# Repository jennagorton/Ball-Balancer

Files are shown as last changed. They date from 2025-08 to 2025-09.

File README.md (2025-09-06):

<h1 align="center">Ball Balancing Robot</h1>
<p align="center">Jenna Gorton, August 2025</p>

<p align="center">
  workingTest
</p>
<p align="center">Stabilizing at center</p>

-----

About 
= 
I designed and built a 3RRS parallel manipulator to stabilize a ball on a platform. To complete this project, I developed the robot in CAD, derived the inverse kinematic model, and used a PID algorithm to control the robot.

Files
=
- **`Main.ino`** - Runs the code on the arduino
- **`InverseKinematics.cpp`** - Uses the target tilt angles of the platform to calculate the servo angles
- **`ScreenControl.cpp`** - Finds the calibrated position of the ball
- **`ServoControl.cpp`** - Handles smooth movement of the servos
- **`PID.cpp`** - Creates the PID equations based on the target point and the current location of the ball

Design
=
This robot was designed using CAD and then 3D printed with PLA
- This robot has a servo to control each leg of the 3RRS parallel manipulator. The lower limb of the leg has a rotational joint attached to the servo and upper limb, and the upper limb connects to the platform with a spherical joint.
- On the platform, there is a 4-wire resistive touch screen to track the position of the ball

Programming
=
The code was written in C++, then compiled and executed through an Arduino sketch
- The inverse kinematic model was hand-derived, and the equations were implemented in C++. The inputs are the height of the platform and the tilt of the platform in the X and Y directions.
- Two PID controllers are running simultaneously, one handles the tilt in the Y direction and the other handles the tilt in the X direction. Different gain constants were used when the ball was near the target and far away. The gain constants were carefully tuned by hand until the movement was smooth and precise.

Patterns
=
Four different pattern modes continuously move the target balance point around the platform. The modes can be changed by pressing a button, and the screen displays the current mode.

| <div align="center">GIF 1<br>**Ellipse Pattern**</div> | <div align="center">GIF 2<br>**Line Pattern**</div> |
|---|---|
| <div align="center">GIF 3<br>**Figure 8 Pattern**</div> | <div align="center">GIF 4<br>**Triangle Pattern**</div> |

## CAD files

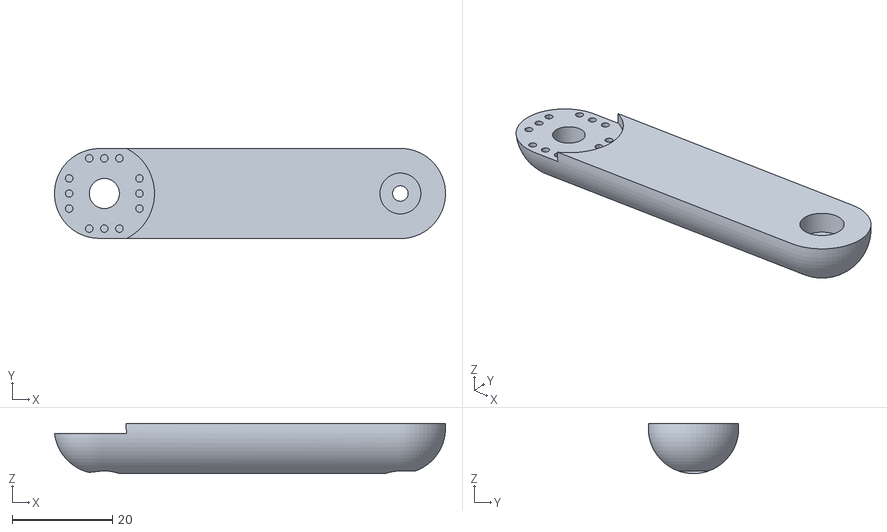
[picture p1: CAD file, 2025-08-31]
STL Files/L1 - Part 1 8.stl
77.9 x 18.0 x 10.0

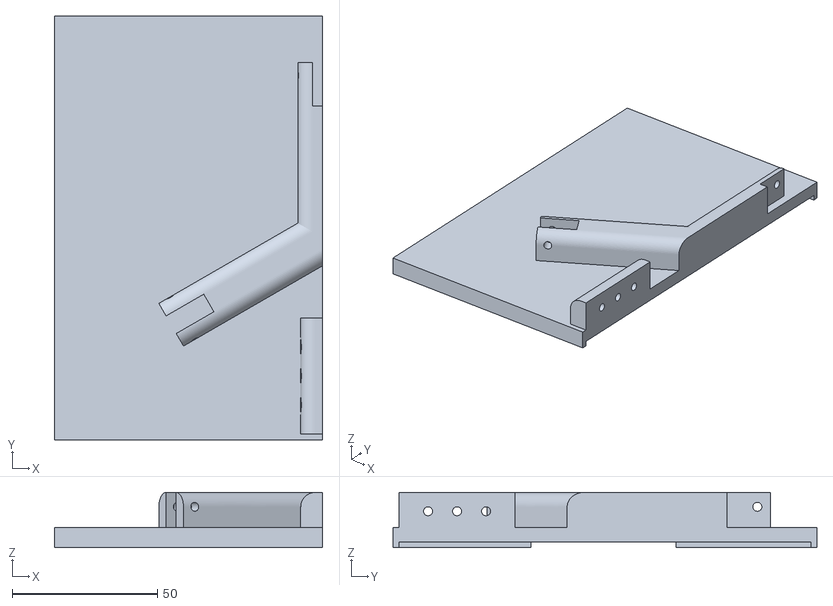
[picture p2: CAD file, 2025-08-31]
STL Files/Platform - Part 2.stl
92.4 x 146.0 x 19.0

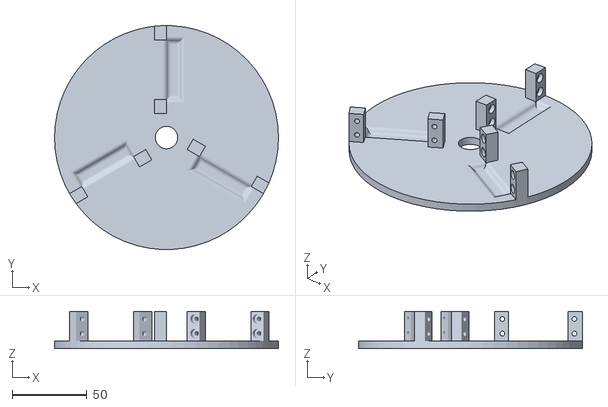
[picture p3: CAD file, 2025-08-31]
STL Files/Base - Part 1 7.stl
150.0 x 149.9 x 25.0

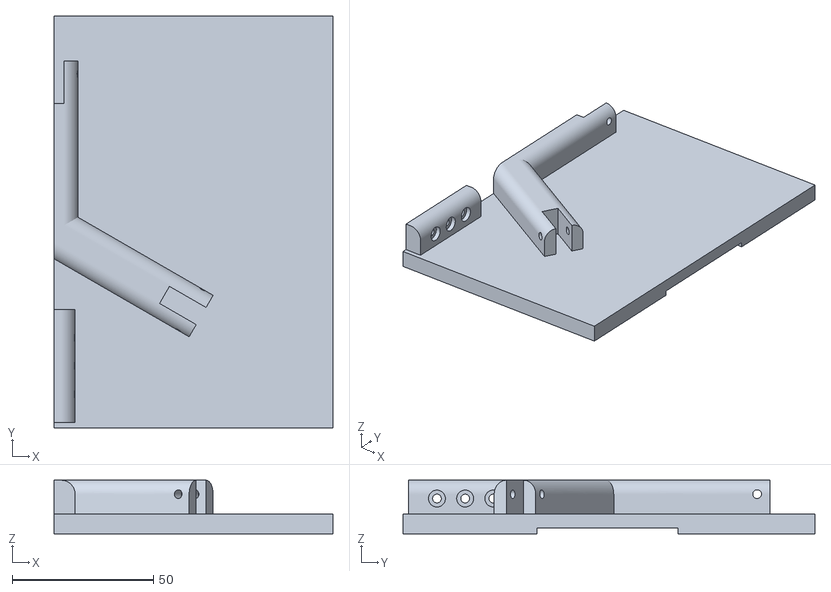
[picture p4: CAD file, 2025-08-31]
STL Files/Platform - Part 1.stl
98.9 x 146.0 x 19.0

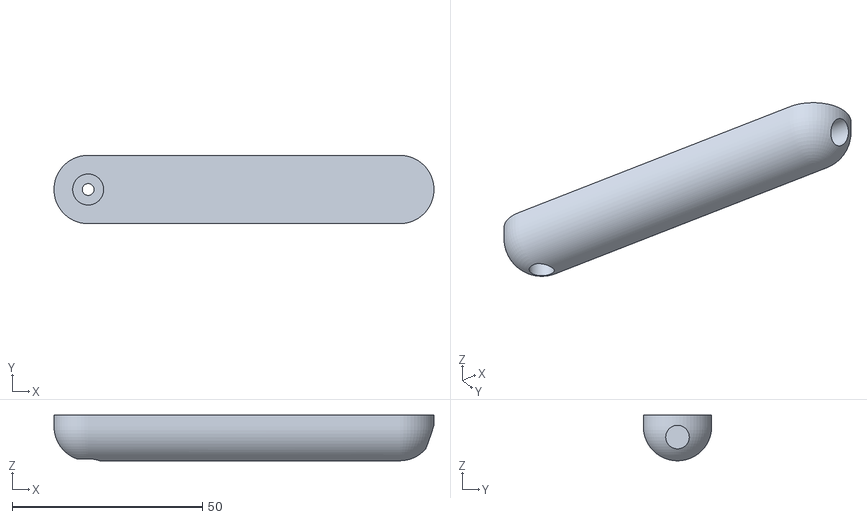
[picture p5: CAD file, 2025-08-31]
STL Files/L2 - Part 1 8.stl
100.0 x 18.0 x 12.0

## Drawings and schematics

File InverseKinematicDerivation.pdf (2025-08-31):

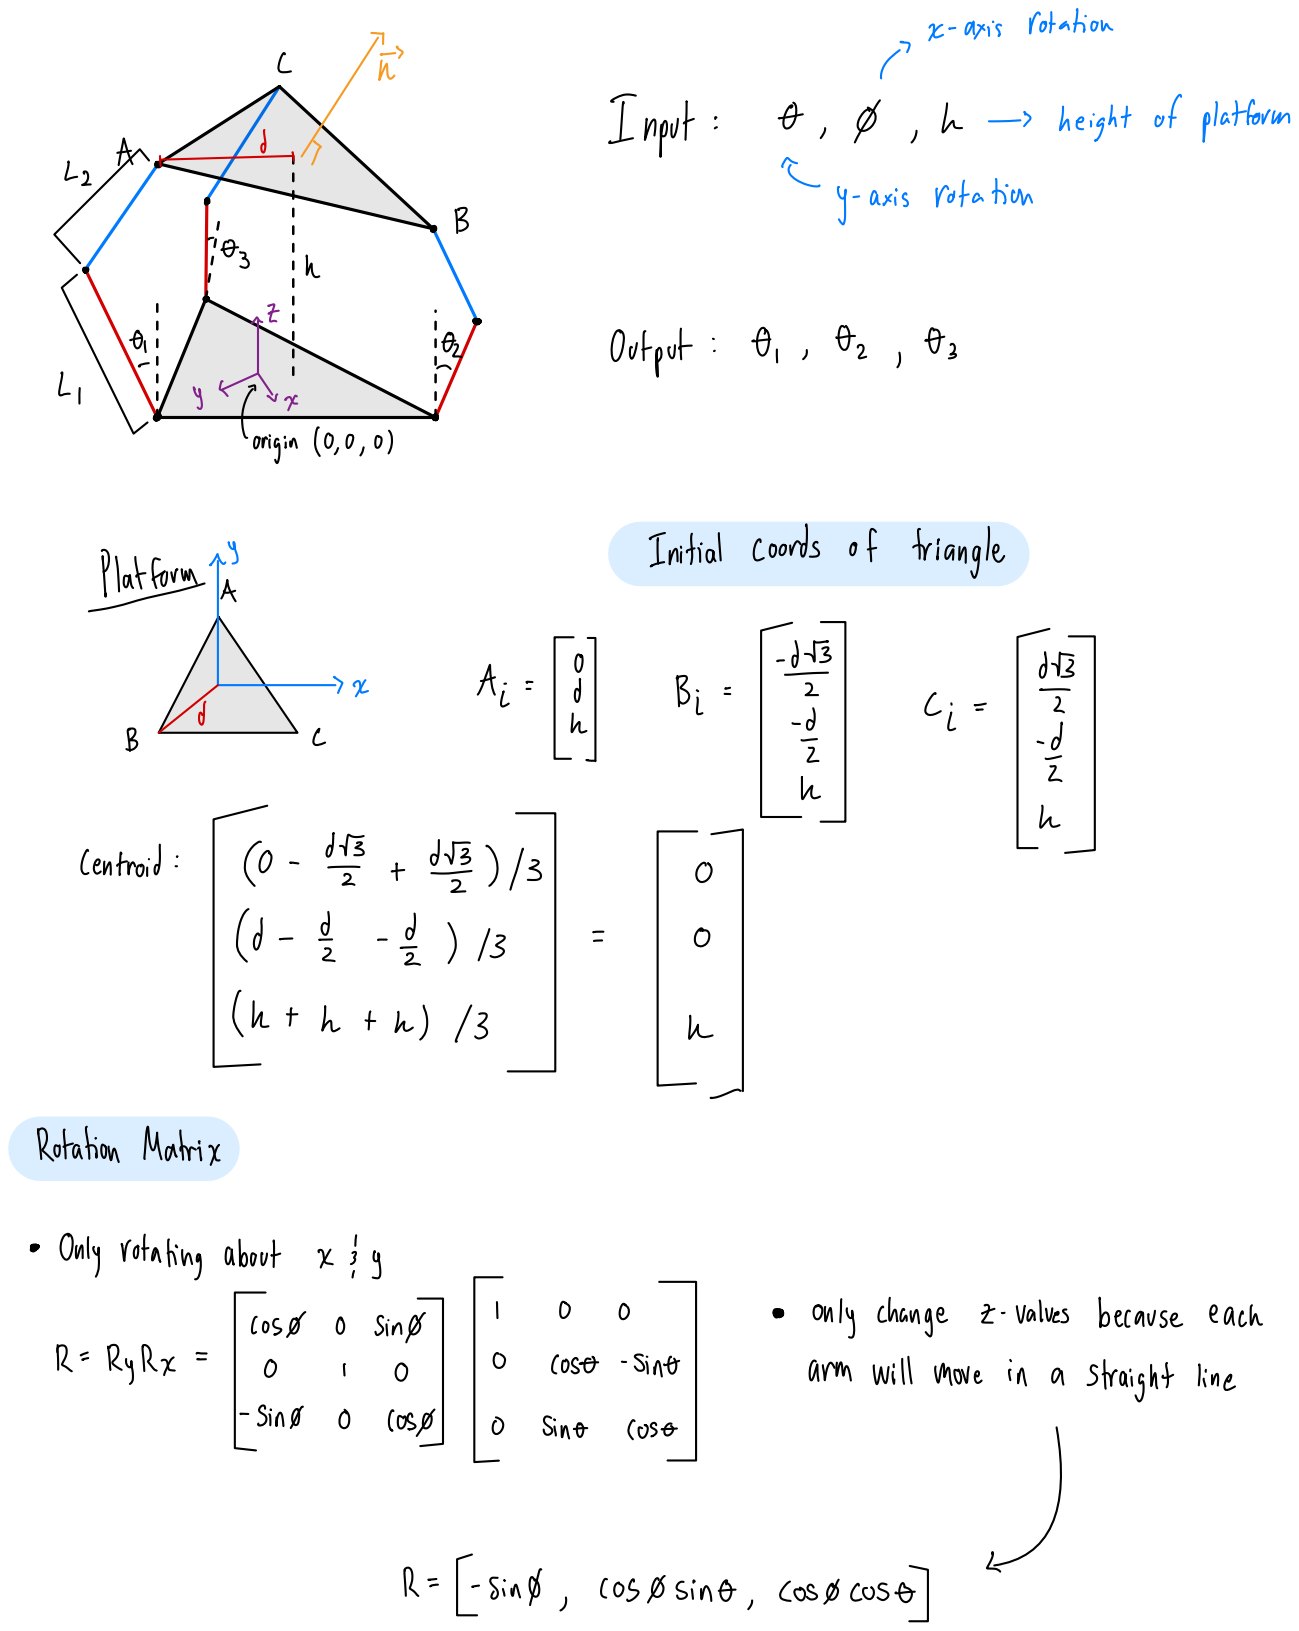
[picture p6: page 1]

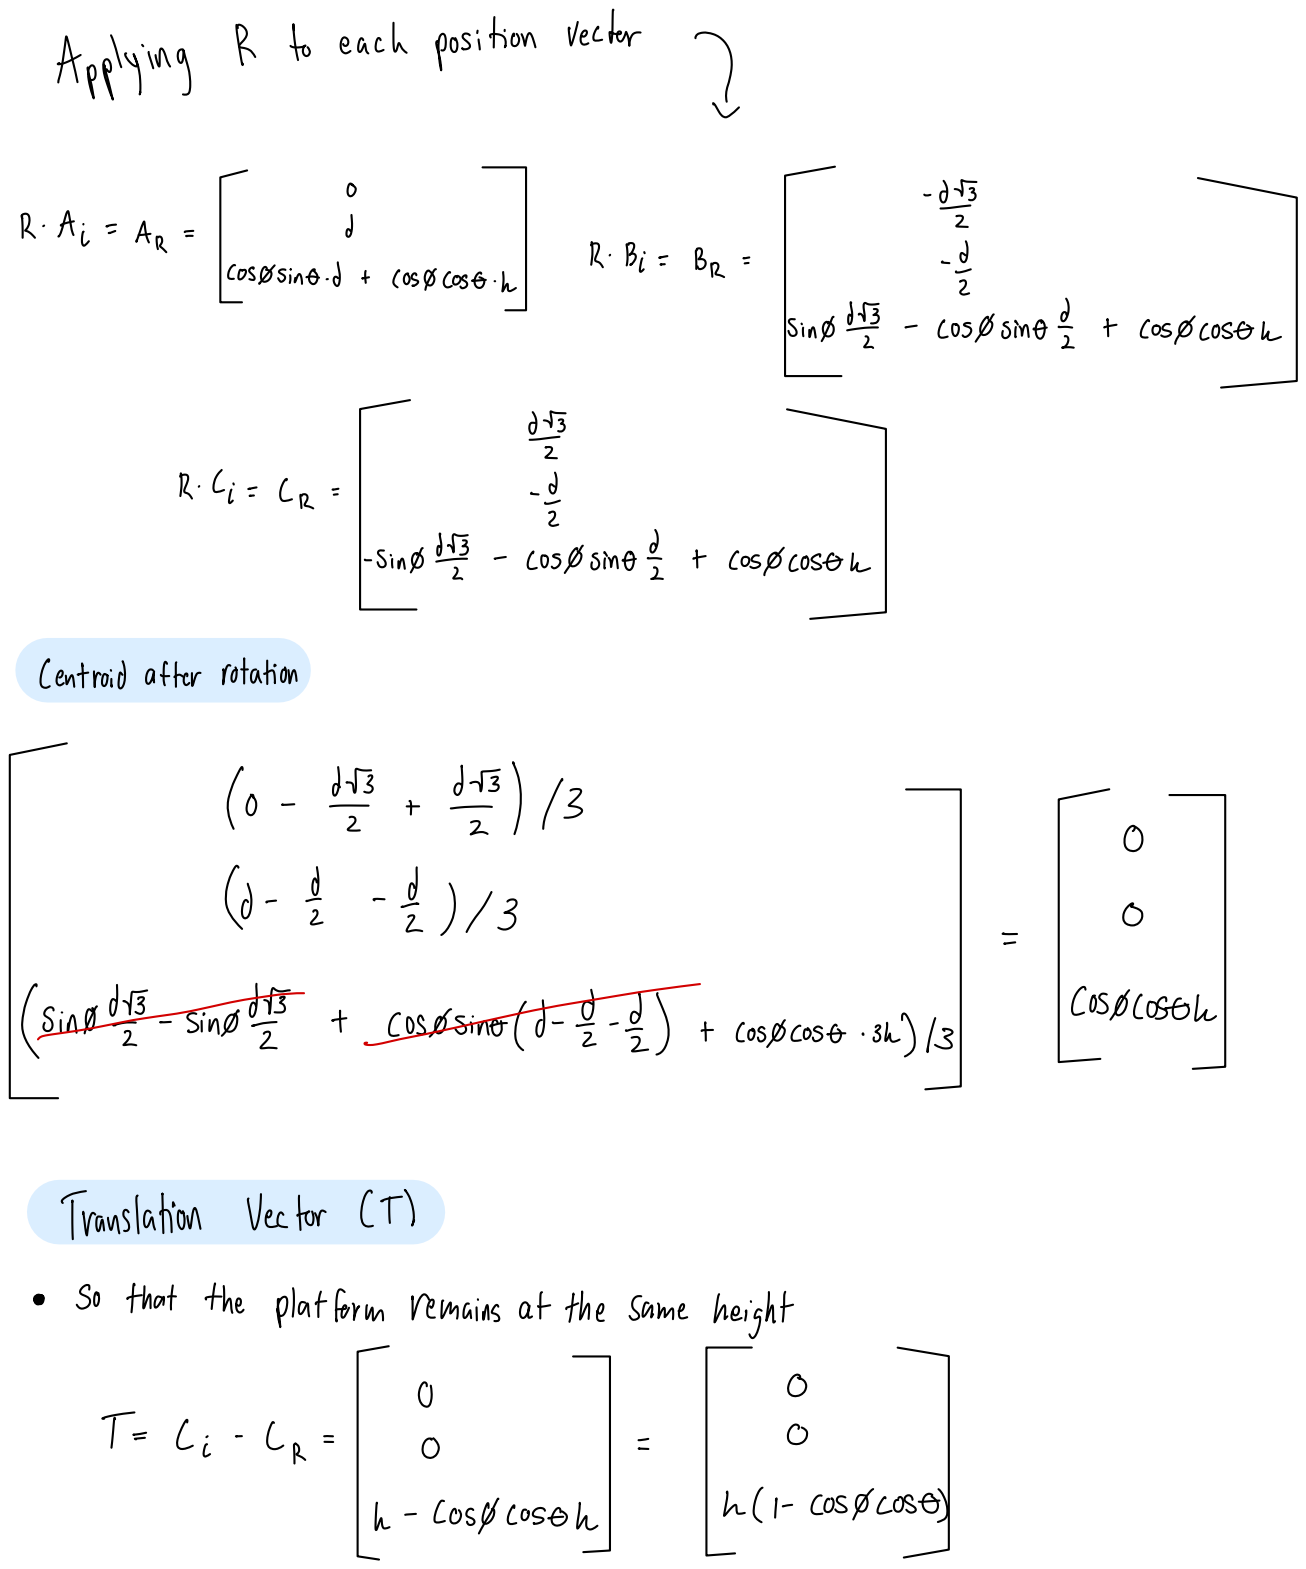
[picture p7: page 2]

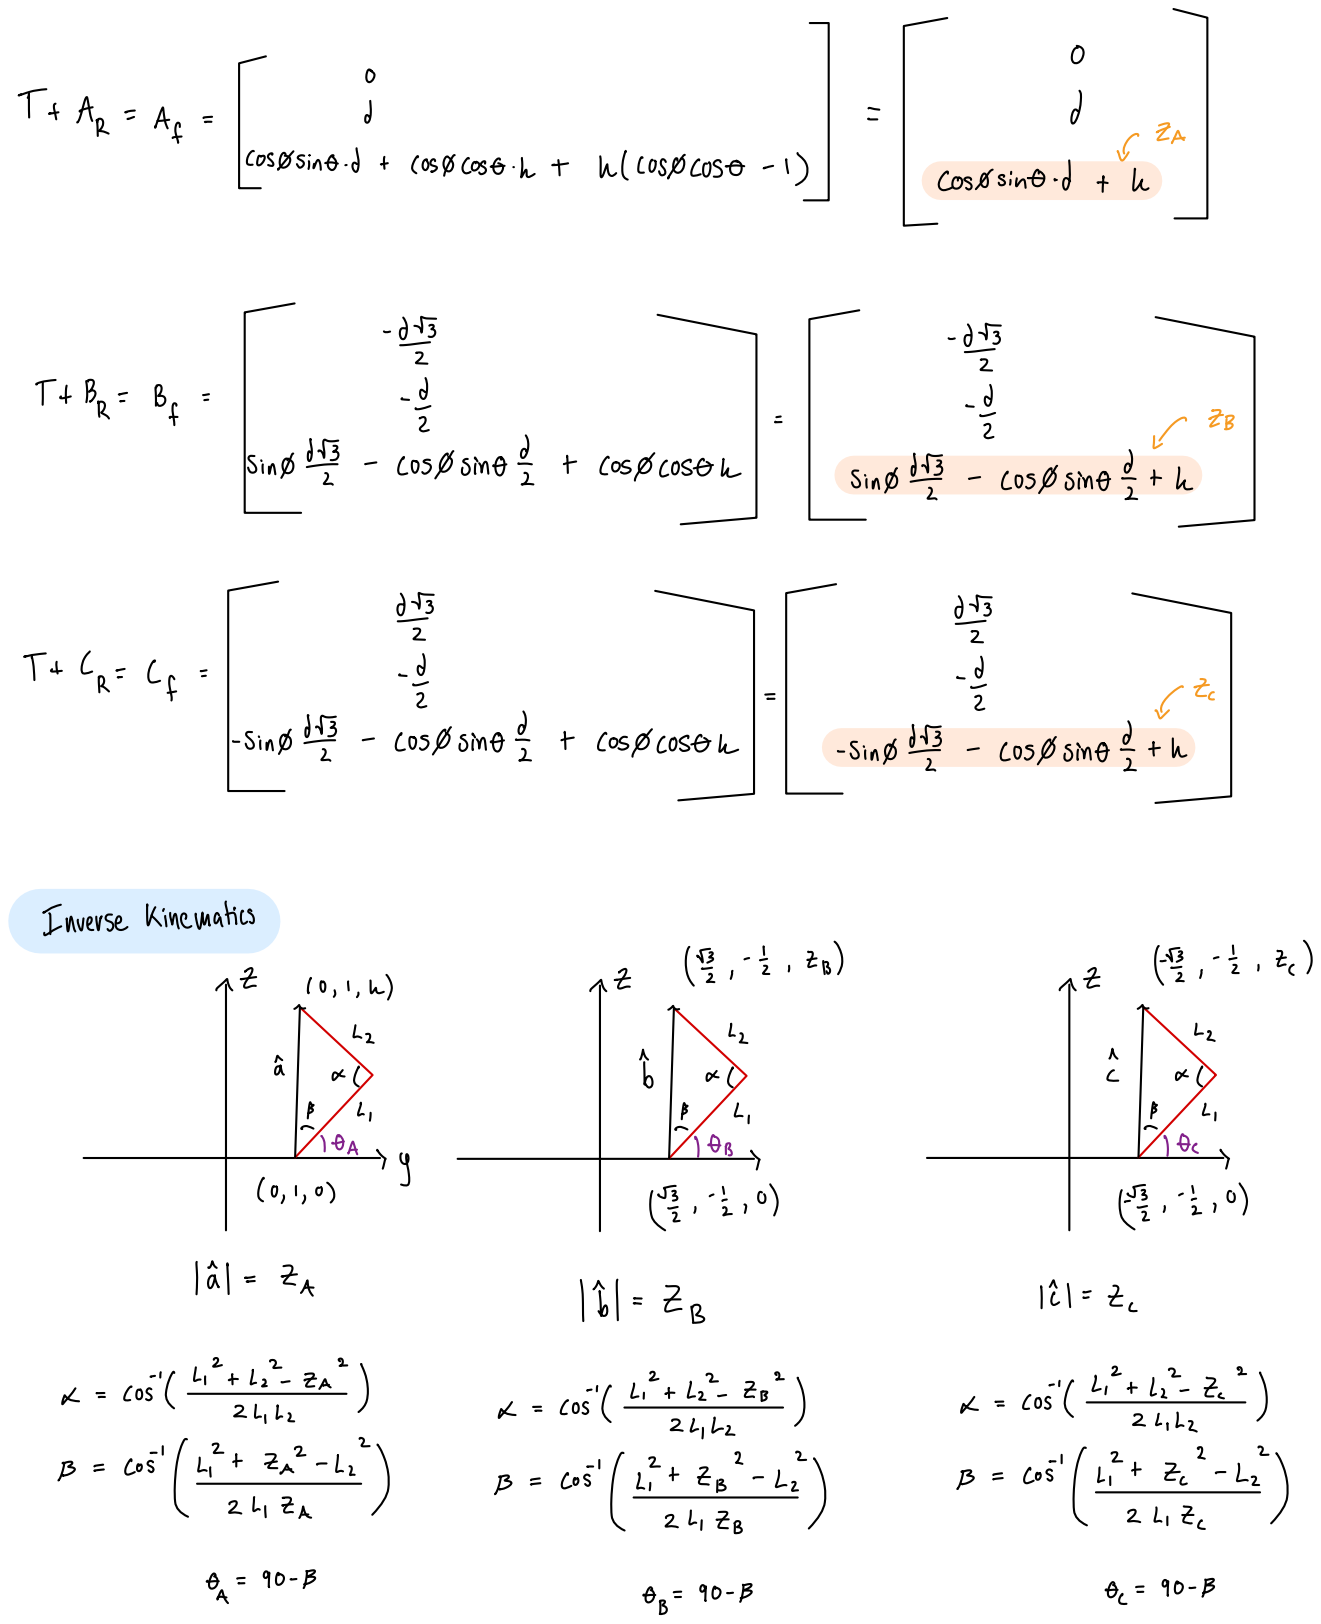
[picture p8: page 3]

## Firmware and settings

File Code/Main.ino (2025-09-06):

#include <Arduino.h>
#include "InverseKinematics.h"
#include "ServoControl.h"
#include "ScreenControl.h"
#include "PID.h"
#include <Wire.h>
#include <Adafruit_GFX.h>
#include <Adafruit_SSD1306.h>

// -------------------- OLED Setup --------------------
#define SCREEN_WIDTH 128
#define SCREEN_HEIGHT 64
Adafruit_SSD1306 display(SCREEN_WIDTH, SCREEN_HEIGHT, &Wire, -1);

const int buttonPin = 2; 
int buttonState = 0;
int lastButtonState = 0;
int mode = 0; // 0=balance, 1=ellipse, 2=line, 3=figure 8, 4=triangle
int lastMode = -1;


void setup() {
  // Initialization functions
  Serial.begin(115200);
  screen_init();
  servo_init();
  pinMode(buttonPin, INPUT_PULLUP);

  if(!display.begin(SSD1306_SWITCHCAPVCC, 0x3C)){
    Serial.println("SSD1306 allocation failed");
    for(;;);
  }
  display.clearDisplay();
}

void loop() {

  buttonState = digitalRead(buttonPin);

  //detects button transition
  if (buttonState == LOW && lastButtonState == HIGH) {
    mode = (mode + 1) % 5;
    Serial.print("Mode changed to: ");
    Serial.println(mode);
    delay(50);              
  }

  if(mode != lastMode){
    updateOLED(mode);
    lastMode = mode;
  }

  //changes pattern based on button press
  switch (mode) {
    case 0:
      balance(0, 0);
      break;
    case 1:
      ellipse(20, 20, 10);
      break;
    case 2:
      line(50, 0, 750);
      break;
    case 3:
      figure8(40, 20, 3);
      break;
    case 4:
      triangle(5); 
      break;
  }

  lastButtonState = buttonState;
}


//function to write to screen
void updateOLED(int mode) {
  display.clearDisplay();
  display.setTextSize(2);
  display.setTextColor(SSD1306_WHITE);

  const char* text;
  switch(mode){
    case 0: text = "Balance"; break;
    case 1: text = "Ellipse"; break;
    case 2: text = "Line"; break;
    case 3: text = "Figure 8"; break;
    case 4: text = "Triangle"; break;
  }

  int16_t x1, y1;
  uint16_t w, h;
  display.getTextBounds(text, 0, 0, &x1, &y1, &w, &h);

  int16_t x = (SCREEN_WIDTH - w) / 2;
  int16_t y = (SCREEN_HEIGHT - h) / 2;

  display.setCursor(x, y);
  display.println(text);
  display.display();
}

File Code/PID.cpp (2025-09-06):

#include <Arduino.h>
#include <math.h>
#include "PID.h"

// PID Constants
#define kp_far_x 0.8
#define ki_far_x 0.15 
#define kd_far_x 0.27

#define kp_far_y 0.6
#define ki_far_y 0.15
#define kd_far_y 0.26

#define kp_close_x .18
#define ki_close_x 0.15
#define kd_close_x 0.23

#define kp_close_y .12
#define ki_close_y 0.15
#define kd_close_y 0.235

#define max_output 83.5  // max X distance away from the center
#define max_angle 12.5   // max tilt angle
const double height = 85; // height of platform

//Array definition
double error[2] = { 0, 0 };
double error_prev[2];
double integral[2] = { 0, 0 };
double derivative[2] = { 0, 0 };
double output[2];
double angles[2];
long time_pattern = 0;

//PID algorithm for x and y
void balance(double target_x, double target_y) {

  // Serial.print("X: ");
  // Serial.print(target_x);
  // Serial.print(", Y: ");
  // Serial.println(target_y);

  static unsigned long t_prev = 0; //previous time
  static unsigned long last_time = 0; //when ball was last detected
  unsigned long t = millis(); //current time
  double dt = (t - t_prev) / 1000.0; //calculated dt

  //inital & time gaps
  if (t_prev == 0 || dt > .075) {
    t_prev = t;
    return; 
  }

  /*************PID CONTROL****************/
  if (dt >= 0.01) {
    
    calibrated_coords p = find_position(); 

    if (detection()) { //only run if ball on plate
      last_time = t;

      double error_current;
      for (int i = 0; i < 2; i++) { // Y:0,   X:1

        error_prev[i] = error[i]; //store error before updating

        //calculating current error
        if (i == 0) {
            error_current = p.y - target_y;
        } else {
            error_current = p.x - target_x;
        }

        error[i] = error_current; //updating with current error

        integral[i] += error[i] * dt; //calculating integral
        integral[i] = constrain(integral[i], -50, 50);  //preventing windup

        derivative[i] = (error[i] - error_prev[i]) / dt; //calculating derivative
        
        if (isnan(derivative[i]) || isinf(derivative[i])) { //checking if valid
          derivative[i] = 0;
        }

        //debug
        //Serial.println(error[0]);
      }

      /*****************PID EQUAIONS******************/ 
      if (abs(error[0]) < 15) { // Y
        output[0] = kp_close_y * error[0] + ki_close_y * integral[0] + kd_close_y * derivative[0]; // differnet gain constants when close and far
      }else{
        output[0] = kp_far_y * error[0] + ki_far_y * integral[0] + kd_far_y * derivative[0];
      }
      if (abs(error[1]) < 25){ // X
        output[1] = kp_close_x * error[1] + ki_close_x * integral[1] + kd_close_x * derivative[1]; 
      }else{
        output[1] = kp_far_x * error[1] + ki_far_x * integral[1] + kd_far_x * derivative[1];
      }
        
      angles[0] = constrain(output[0], -max_output, max_output) * (max_angle / max_output);  // mapping raw output to serov angle
      angles[1] = constrain(output[1], -max_output, max_output) * (max_angle / max_output);  
    
      unsigned long start = millis();
      while (millis() - start < 20) { // run for long enough that motion seems smooth
        move(angles[0], -angles[1], height); //phi negative because of screen orientation
      }
    }

    else {
      // if no input for 3 sec reset
      if (t - last_time >= 3000) {
        integral[0] = integral[1] = 0;
        move(0, 0, height);
      }
    }
    t_prev = t;
  }
}

/***************** LINE *******************/
int direction = 0;
unsigned long lastSwitch = 0;

void line(double rx, double ry, unsigned long interval) {
  unsigned long now = millis();

  // switch direction after interval
  if (now - lastSwitch >= interval) {
    direction = !direction;   // flip 0 ↔ 1
    lastSwitch = now;
  }

  // flip direction
  if (direction == 0) {
    balance(rx, ry);
  } else {
    balance(-rx, -ry);
  }
}

/***************** TRIANGLE *******************/
void triangle(int scale) {
  unsigned long now = millis();

  if (now - lastSwitch >= 900) {
    direction = (direction + 1) % 3; 
    lastSwitch = now;
  }

  //flip direction
  if (direction == 0) {
    balance(0, scale * 10);
  } else if (direction == 1) {
    balance(scale * -10, -20);
  } else if (direction == 2) {
    balance(scale * 10, -20);
  }

}

/***************** FIGURE 8 *******************/
double theta = 0;
unsigned long lastStep = 0;

void figure8(double r, int wait, int num) {
  unsigned long now = millis();

  if (now - lastStep < wait) return; //controls speed
  lastStep = now;

 
  double scale = r * (2 / (3 - cos(2 * theta)));
  double x = scale * cos(theta);
  double y = scale * sin(2 * theta) / 1.5;

  
  balance(x, y); //move

  theta += 0.05;
  if (theta >= 2 * PI) theta = 0;  // wrap around
}

/***************** ELLIPSE *********************/
void ellipse(double rx, double ry, int interval) {
  unsigned long now = millis();

  if (now - lastStep >= interval) {
    lastStep = now;

    balance(rx * cos(theta), ry * sin(theta)); //moves
    theta += 0.1;
    if (theta >= 2 * PI) {
      theta = 0; // wrap around
    }
  }
}

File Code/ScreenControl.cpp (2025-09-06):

#include "ScreenControl.h"
#include <Arduino.h>

#define YP A1
#define XM A2
#define YM 7
#define XP 6


// Touch Screen usable values
#define MIN_X 60
#define MAX_X 970
#define MIN_Y 95
#define MAX_Y 940

// Screen dimensions
#define WIDTH 187.0
#define HEIGHT 140.0

// Pressure thresholds (adjust if needed)
#define MINPRESSURE 10
#define MAXPRESSURE 500

TouchScreen ts = TouchScreen(XP, YP, XM, YM, 300);  // 300 = ohms of touchscreen
TSPoint raw_val;


/***********************ARDUINO MAP FUNCTION**************************/
// long map(long x, long in_min, long in_max, long out_min, long out_max) {
//   return (x - in_min) * (out_max - out_min) / (in_max - in_min) + out_min;
// }

//Recreating map function to avoid integer math, need more exact results
double map_double(double x, double in_min, double in_max, double out_min, double out_max) {
  return (x - in_min) * (out_max - out_min) / (in_max - in_min) + out_min;
}


void screen_init() {
  pinMode(XM, OUTPUT);
  pinMode(YP, OUTPUT);
}

//checks if theres an object on touchscreen
bool detection() {
  raw_val = ts.getPoint();
  pinMode(XM, OUTPUT);
  pinMode(YP, OUTPUT);
  
  // if x in range then ball on plate
  return (raw_val.x > 0 && raw_val.x < 1023);
}

// calculating usable coordinates of balls positon
calibrated_coords find_position() {
  static double last_x = 0;
  static double last_y = 0;
  calibrated_coords cali_p;

  raw_val = ts.getPoint();
  pinMode(XM, OUTPUT);
  pinMode(YP, OUTPUT);


  //mapping the raw values to the usable range
  double x_coords = map_double(raw_val.x, MIN_X, MAX_X, WIDTH / 2, -WIDTH / 2);
  double y_coords = map_double(raw_val.y, MIN_Y, MAX_Y, HEIGHT / 2, -HEIGHT / 2);

 
  last_x = x_coords;
  last_y = y_coords;
  cali_p.x = x_coords;
  cali_p.y = y_coords;
  cali_p.z = raw_val.z;


  return cali_p;
}
